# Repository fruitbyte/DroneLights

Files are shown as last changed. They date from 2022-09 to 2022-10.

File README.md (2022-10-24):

<h1 align="center">DroneLights</h1>
<h3 align="center">A really bright light for your drone</h3>


---

Drone lights help light up your aircraft for night flying and ease of observation in the daytime. This specific drone light PCB also doubles as a simple breakout board for the ATTiny84A. This was built so that [UBC UAS](https://www.ubcuas.com/) can fly and test whenever the weather cooperates!

## Project Directory
- Manuals: PCB Assembly/Programming Info
- PCB: KiCad project files (KiCad 6.0+)
- Programming: Code for the ATTiny84A

## Features
- On/Off switch
- Breakout pins for ATtiny84A prototyping
- Labelled programming pins
- Programmable pin LED
- On indicator
- Reset and configurable pushbuttons
- Adjustable brightness and blink interval
- External input
- Zip-tie-able

## Warnings
Please build and test with caution. Do not look directly into the light at any point when testing. May cause eye damage.

## To Do
### Code
- [ ] Add different blink modes, toggled by signal pin beside power port/I2C/SPI
- [ ] Get rid of press and hold for mode switch (instead of delays in main loop, use millis function), use some form of debounce

### PCB Rev B Notes
- [ ] Add a 5V fuse to protect sensitive components
- [ ] Add diode markings to silkscreen
- [ ] Fix incorrectly labelled MOSI/MISO silkscreen on programming pins
- [ ] Use proper header spacing on breakout pins so that headers can be soldered if desired
- [ ] Remove unnecessary components for compact version (programming, breakouts, unnecessary diodes, etc.)
- [ ] Use a smaller toggle sliding switch for SW3

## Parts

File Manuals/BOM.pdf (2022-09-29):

Item | Qty | Reference(s) | Value | Digikey No.
1 | 1 C1 | | 0.1 uF | 445-1314-1-ND
2 | 1 D1 | | LED
3 | 2 D2, D3 | | RED LED | 3147-B1911USD-20D000114U1930CT-ND
4 | 4 H1, H2, H3, H4 | | M3
5 | 12 J1, J3, J4, J5, J6, J7, J8, J9, J11, J12, J13, J14 | | Proto Pin
6 | 1 J2 | | Input
7 | 1 J10 | | Prog_Connector
8 | 2 JP1, JP2 | | OpenJumper
9 | 1 MOSFET1 | | T2N7002BK | T2N7002BKLMCT-ND
10 | 1 R1 | | 10 | P10.0HCT-ND
11 | 3 R2, R3, R4 | | 10k | RNCP0603FTD10K0CT-ND
12 | 1 R5 | | 4k7 | 2019-RK73H1JRTTD4701FCT-ND
13 | 2 SW1, SW2 | | CT11024.3F160 | 2449-CT11024.3F160-ND
14 | 1 SW3 | | GF-123-0054 | CWI333-ND
15 | 1 U1 | | ATTINY84A-PU | ATTINY84A-PU-ND

MPN | Red MPN | White MPN | Green MPN
C1608X7R1H104K080AA
| XPEBRD-L1-0000-00501 | XPEBWT-L1-0000-00C51 | XPEBGR-L1-0000-00F01
B1911USD-20D000114U1930

T2N7002BK,LM
ERJ-3EKF10R0V
RNCP0603FTD10K0
RK73H1JRTTD4701F
CT11024.3F160
GF-123-0054
ATTINY84A-PU

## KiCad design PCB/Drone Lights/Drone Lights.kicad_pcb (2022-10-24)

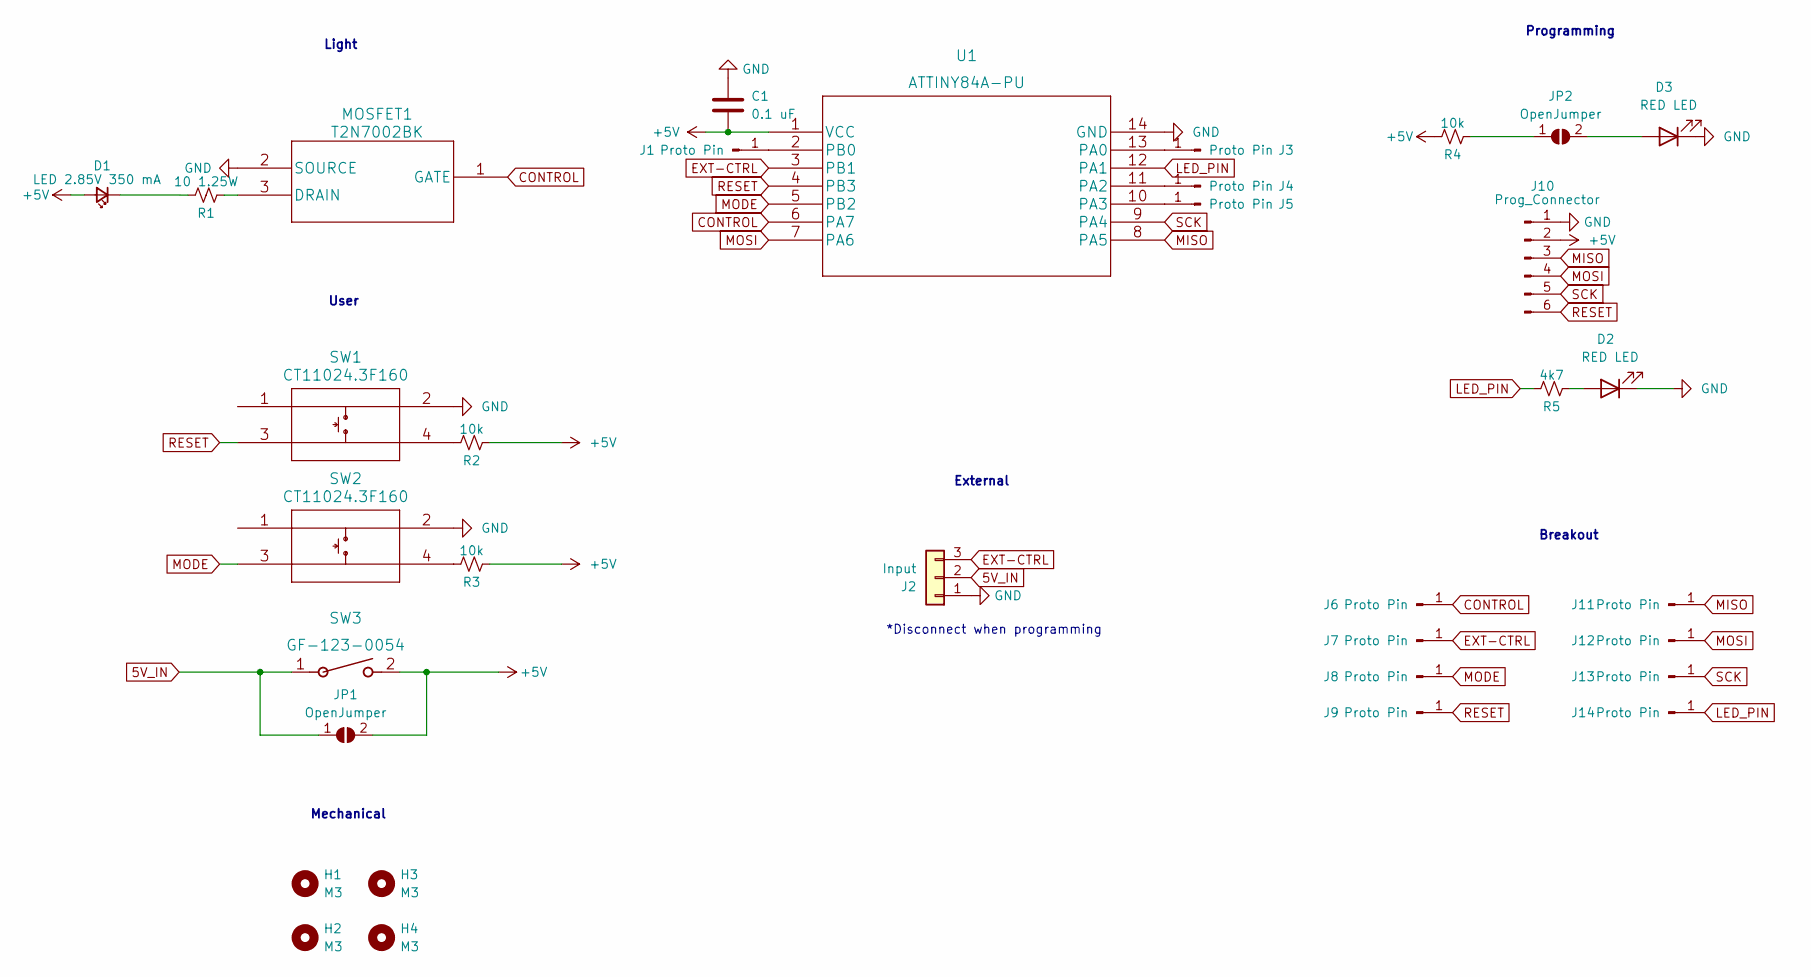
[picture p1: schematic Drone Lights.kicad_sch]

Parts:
C1: 0.1 uF; C_0603_1608Metric_Pad1.08x0.95mm_HandSolder; MPN C1608X7R1H104K080AA; Digikey No. 445-1314-1-ND
D1: LED 2.85V 350 mA; XLAMP_LED_XPE2
D2, D3: RED LED; R_0603_1608Metric_Pad0.98x0.95mm_HandSolder; MPN B1911USD-20D000114U1930; Digikey No. 3147-B1911USD-20D000114U1930CT-ND
H1, H2, H3, H4: M3; MountingHole_3.2mm_M3
J1, J3, J4, J5, J6, J7, J8, J9, J11, J12, J13, J14: Proto Pin; Pin_D1.0mm_L10.0mm
J2: Input; PinHeader_1x03_P2.54mm_Vertical
J10: Prog_Connector; PinHeader_1x06_P2.54mm_Vertical
JP1, JP2: OpenJumper; SolderJumper-2_P1.3mm_Open_RoundedPad1.0x1.5mm
MOSFET1: T2N7002BK; MPN T2N7002BK,LM; Digikey No. T2N7002BKLMCT-ND
R1: 10 1.25W; R_0603_1608Metric_Pad0.98x0.95mm_HandSolder; MPN CRGP2010F10R; Digikey No. A130636CT-ND
R2, R3, R4: 10k; R_0603_1608Metric_Pad0.98x0.95mm_HandSolder; MPN RNCP0603FTD10K0; Digikey No. RNCP0603FTD10K0CT-ND
R5: 4k7; R_0603_1608Metric_Pad0.98x0.95mm_HandSolder; MPN RK73H1JRTTD4701F; Digikey No. 2019-RK73H1JRTTD4701FCT-ND
SW1, SW2: CT11024.3F160; MPN CT11024.3F160; Digikey No. 2449-CT11024.3F160-ND
SW3: GF-123-0054; MPN GF-123-0054; Digikey No. CWI333-ND
U1: ATTINY84A-PU; MPN ATTINY84A-PU; Digikey No. ATTINY84A-PU-ND

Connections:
5V_IN: J2.2, JP1.1 (A), SW3.1
+5V: C1.1, D1.2 (A), J10.2, JP1.2 (B), R2.2, R3.2, R4.1, SW3.2, U1.1 (VCC)
CONTROL: J6.1, MOSFET1.1 (GATE), U1.6 (PA7)
EXT-CTRL: J2.3, J7.1, U1.3 (PB1)
GND: C1.2, D2.1 (K), D3.1 (K), J2.1, J10.1, MOSFET1.2 (SOURCE), SW1.2, SW2.2, U1.14 (GND)
LED_PIN: J14.1, R5.1, U1.12 (PA1)
MISO: J10.3, J11.1, U1.8 (PA5)
MODE: J8.1, SW2.3, U1.5 (PB2)
MOSI: J10.4, J12.1, U1.7 (PA6)
unnamed: D1.1 (K), R1.1
unnamed: D2.2 (A), R5.2
unnamed: D3.2 (A), JP2.2 (B)
unnamed: J1.1, U1.2 (PB0)
unnamed: J3.1, U1.13 (PA0)
unnamed: J4.1, U1.11 (PA2)
unnamed: J5.1, U1.10 (PA3)
unnamed: JP2.1 (A), R4.2
unnamed: MOSFET1.3 (DRAIN), R1.2
unnamed: R2.1, SW1.4
unnamed: R3.1, SW2.4
RESET: J9.1, J10.6, SW1.3, U1.4 (PB3)
SCK: J10.5, J13.1, U1.9 (PA4)

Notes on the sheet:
Programming
User
External
Light
*Disconnect when programming
Mechanical
Breakout

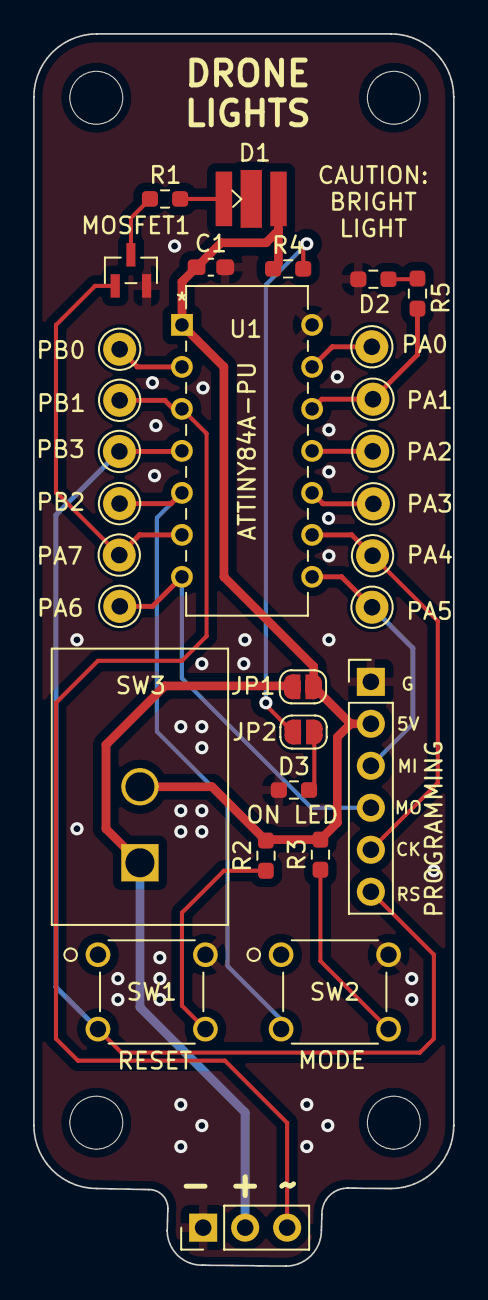
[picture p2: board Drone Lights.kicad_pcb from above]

Board: 2 copper layers, 25.4 x 74.5 mm, 34 parts (0 on the bottom side), 22 nets.

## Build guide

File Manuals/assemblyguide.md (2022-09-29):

# Manufacturing and Assembly Guide
Last updated: September 28, 2022

## Manufacturing
The manufacturing files (gerber and drill) of Rev A can be found in `PCB\Drone Lights\manufacturing_files.zip`. You should be able to upload these to an online manufacturer site and submit the order. These files can also be generated from the `Drone Lights.kicad_pcb` file.

## PCB Assembly

A bill of materials (`Manuals\BOM.pdf`) is available for your reference. You should also have the KiCad project open, as there are some errors in the silkscreen (to be fixed in next revision, will be noted in the instructions below).

### 1. Component Selection
You can add/remove features of this board as desired. Here are some groups of components you will need in order to get the board to work.

Basic drone light blink:
- D1 (pick either green, red, or white)
- R1
- MOSFET1
- U1
- C1

On/Off switch:
- Either connect SW3 __or__ JP1
    - JP1 is connected by soldering the pads together, which bypasses SW3
    - SW3 can be used as an on/off toggle if you have the drone powered but don't want the lights on

Reset button:
- [Optional] Connect SW1 and R2

Mode button:
- [Optional] Connect SW2 and R3

"On" LED:
- [Optional] Connect R4, JP2, and D3

Programming Connector:
- [Optional if you pre-program U1] Connect headers to J10

Programmable pin LED:
- [Optional] Connect R5, D2

### 2. Soldering Components
Some general advice: start by soldering all the SMD components and __make sure your LED polarity is correct or the board will not function__. This revision does not have markings on the silkscreen for polarity, so double check with the board file and the corresponding LED's datasheet (sorry!). Passive components such as the chip resistors and capacitor do not have polarity.

Next, connect all the required jumper pads.

Lastly, solder on the through-hole components. It is easiest to go from shortest/smallest components to largest. Make sure to pre-program U1 (the ATtiny84A) unless you are using the programming port.

### 3. Checks!

Check all solder connections before plugging anything in! Look for things like solder balls connecting adjacent pins, make sure the solder has reflowed properly to make good solder joints, and test continuity with a multimeter.

## Programming
Please note that the board programming pins have an error on the silkscreen:
- MO should be MISO
- MI should be MOSI

An easy guide for flashing the program onto the ATtiny can [found here](https://www.sparkfun.com/news/2237). This requires you to configure an Arduino to be used as an ISP. The "SS" pin in the tutorial is also the "RS" pin on the board's programming port.

Simple blink code with a brightness toggle can be found in `Programming\navlights\navlights.ino`. Note that brightness switching in this implementation requires the Mode button present on the board (see PCB Assembly). More info is in the code comments.

## Mechanical
There are 4 M3 holes on the corners of this PCB which can be used for mounting. They also have a smooth plane between them for you to attach two zipties width-wise to tie the board to your location of choice. Just make sure that if you are pressing the board up against a conductive surface, the contacts on the back of the board are properly insulated from potential shorts.

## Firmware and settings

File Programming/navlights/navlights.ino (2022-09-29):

#define LED_PIN 7
#define MODE_PIN 8

int brightness = 20;
int mode = 0;

void setup() {
  pinMode(LED_PIN, OUTPUT);
}

void loop() {
  // Press and hold "MODE" button until brightness changes to cycle modes
  if(digitalRead(MODE_PIN) == LOW) {
    if (mode < 3) {
      mode++;
    } else {
      mode = 0;
    }
    delay(150);
  }

  // Brightness can be set from 0-255, however 255 is very bright - test with caution aka do not look directly at the light
  switch (mode) {
    case 0:
      brightness = 5;
      break;
    case 1:
      brightness = 20;
      break;
    case 2:
      brightness = 50;
      break;
    case 3:
      brightness = 125;
      break;
  }

  // Blink LED 0.5Hz
  analogWrite(LED_PIN, brightness);
  delay(1000);
  analogWrite(LED_PIN, 0);
  delay(1000);
}

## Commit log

2022-09-29 Init structure
    [Drone Lights.kicad_pcb, Drone Lights.kicad_sch]
2022-09-29 Updated assembly guide
    [Drone Lights.kicad_sch]
2022-09-29 Assemblyguide updates
2022-10-24 Updated with local copy
    [Drone Lights.kicad_pcb, Drone Lights.kicad_sch]

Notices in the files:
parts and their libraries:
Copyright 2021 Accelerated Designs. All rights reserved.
